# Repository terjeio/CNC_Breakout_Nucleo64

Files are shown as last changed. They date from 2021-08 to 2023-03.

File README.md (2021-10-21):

## CNC Breakout board for Nucleo-64 based development boards using ST morpho extension header

[grblHAL driver](https://github.com/grblHAL/STM32F4xx) support for [Nucleo F411RE](https://www.st.com/en/evaluation-tools/nucleo-f411re.html) and [Nucleo F446RE](https://www.st.com/en/evaluation-tools/nucleo-f446re.html) development boards.

**NOTE:** design files are in [KiCad 5](http://www.kicad.org/) format!

**Features:**

* Four layer board

* 4-axis motor support with separate enable for all axes.

* On-board sockets for Polulu \(A4998 and DRV8825\) or Trinamic \(TMC2130 or TMC5160 - SPI mode, TMC2209 - UART mode\) style motor driver modules.

* Opto-coupled limit and signal inputs (X, Y, Z, A, Probe, Reset/E-Stop, Door, Feed Hold and Cycle Start).

* Opto-coupled signal outputs \(Spindle on, Spindle direction, Flood, Mist, Aux0 and Aux1\).
Outputs are open drain \(ULN2003\) capable of draining 500mA, enough to drive most relays directly.

* Jumper selectable drive voltage for inputs and outputs, either 5V internally supplied or 5-30V externally supplied. 
If externally supplied inputs and outputs can be made galvanically isolated from the controller via jumper settings.

* 5V buffered PWM output for spindle speed control.

* Optional optocoupled DC spindle output, can be made galvanically isolated via jumper setting. External supply voltage limited to rating of filtering capacitor C7 (max. 30V).

* I2C port with jumper selectable drive voltage \(3.3V or 5V\). This is complemented with a 5V tolerant input pin that may be used as an interrupt source, eg. for the strobe signal from a I2C-based keypad.

* Two GPIO ports, with two pins each. One is unbuffered and can be used for serial communincation, eg. for MPG or VFD control. One is input only and has 5V tolerant pins.

* Optional on-board EEPROM/FRAM for persistent storage of settings.

* SPI based SD-card interface. If not in use some or all pins may be used as GPIO or as a generic SPI interface with one chip select line, depending on motor drivers used.

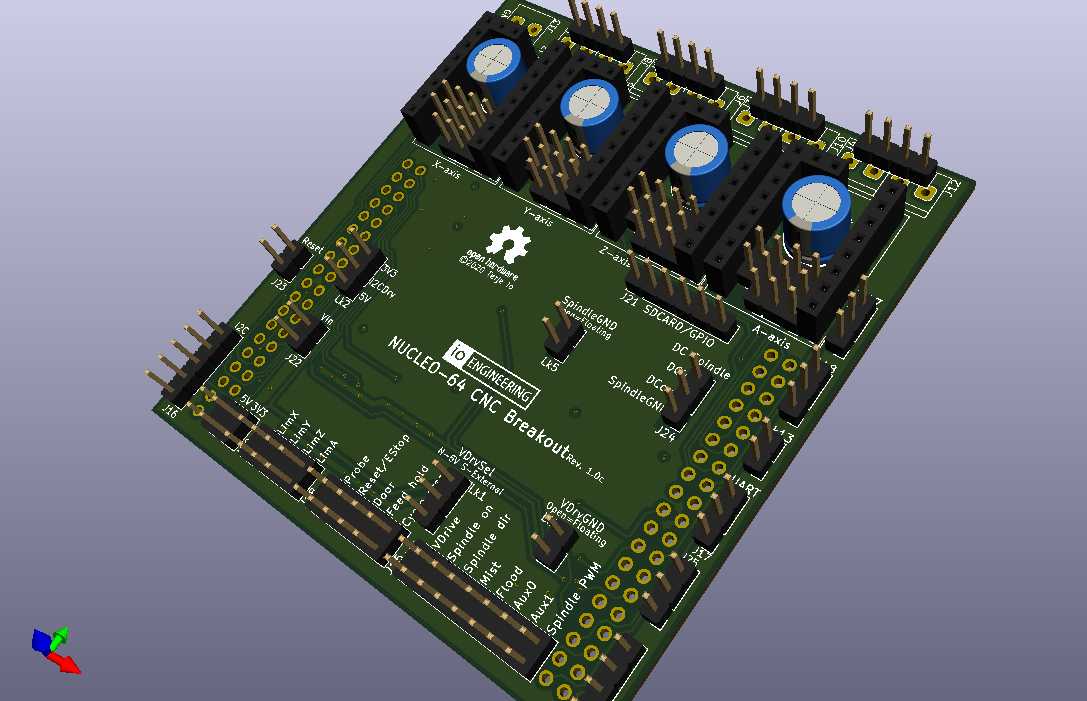
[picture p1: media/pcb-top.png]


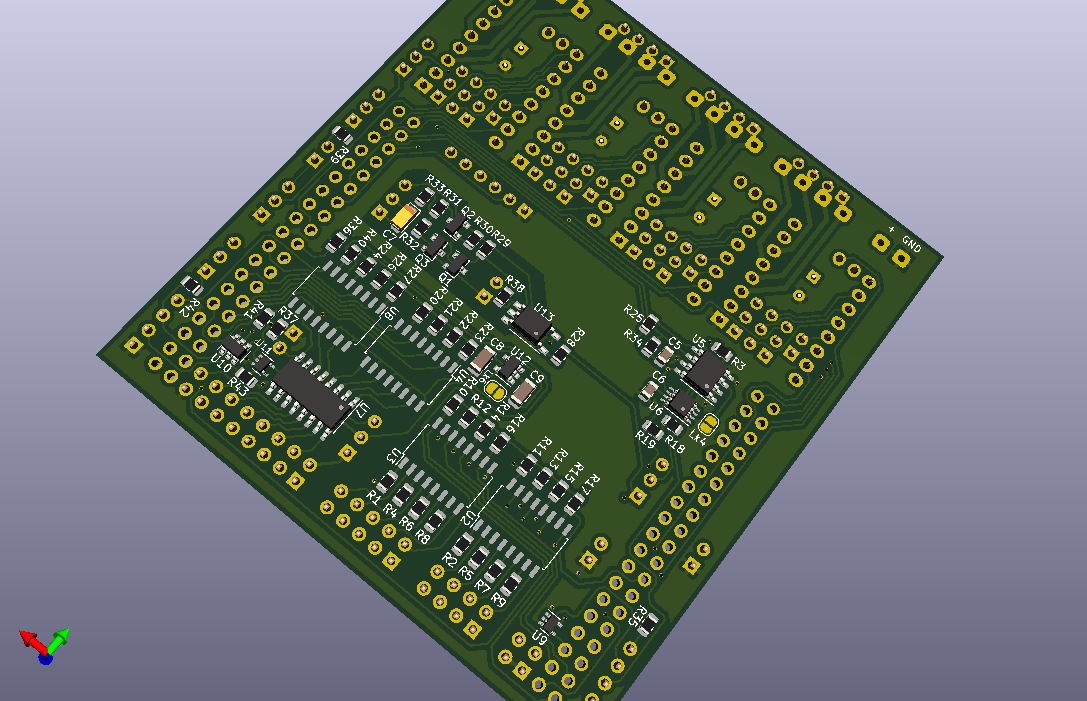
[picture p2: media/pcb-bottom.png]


---

I have a number of _bare_ boards available:

* 1.0 \(preliminary version\): 7 pcs. These do not support Trinamic drivers in SPI/UART mode and has a couple of correctable routing errors in the spindle PWM -> spindle DC circuit. Price: shipping at cost.

* 1.0b: 2 pcs. Price: EUR 5/pcs + shipping at cost. These are missing a pullup resistor for the keypad strobe input - this _may_ affect operation of the keypad plugin. Easy to add externally.

These boards are gold plated \(ENIG finish\).

* 1.0c: \(current version\) Not yet available.

I do not plan to offer populated boards as either I have to solder them myself \(will be expensive\) or place an order for ready made boards \(with only SMD components soldered\).  
A redesign is likely required for ready made boards as some of the components may not be available from the standard selection offered by e.g. [JLPCB](https://jlcpcb.com/).

It would be great if someone would get populated boards made and offered for sale as I am currently not prepared to do that.

---

2021-08-22

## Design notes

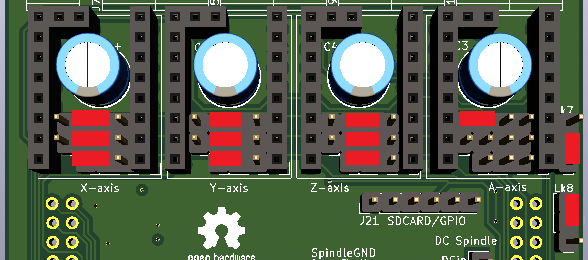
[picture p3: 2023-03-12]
media/TMC_SPI_mode_3motors.png

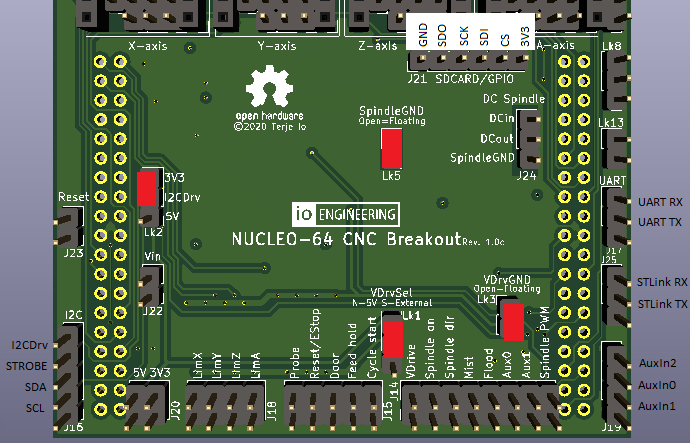
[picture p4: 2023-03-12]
media/Basic.png

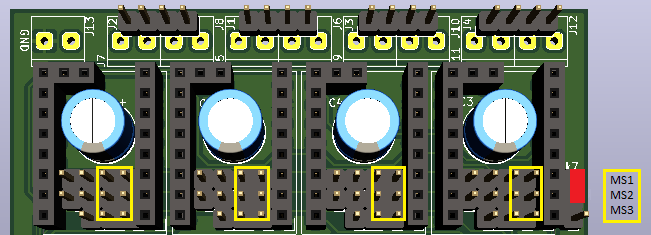
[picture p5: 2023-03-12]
media/Normal.png

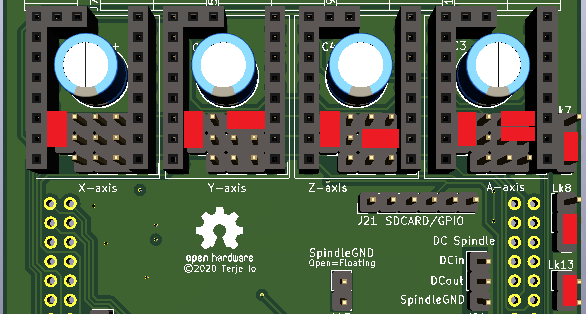
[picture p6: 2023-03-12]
media/TMC_UART_mode.png

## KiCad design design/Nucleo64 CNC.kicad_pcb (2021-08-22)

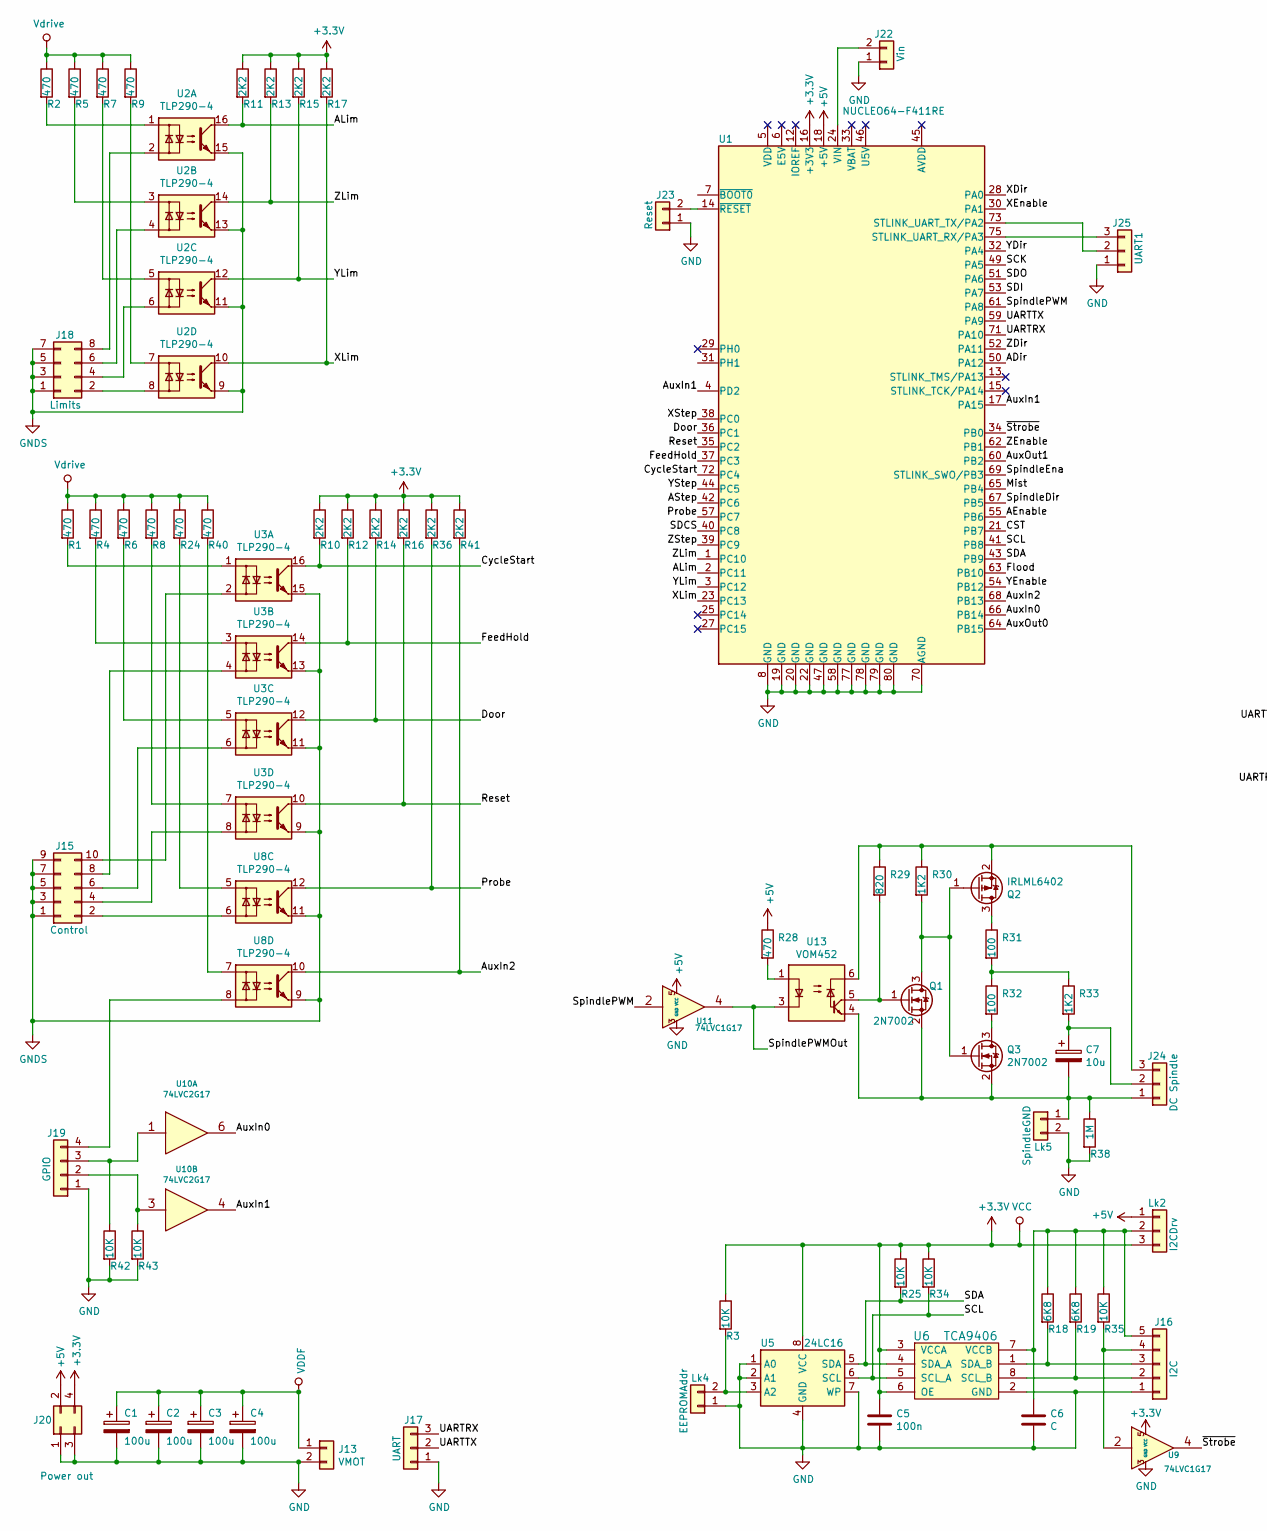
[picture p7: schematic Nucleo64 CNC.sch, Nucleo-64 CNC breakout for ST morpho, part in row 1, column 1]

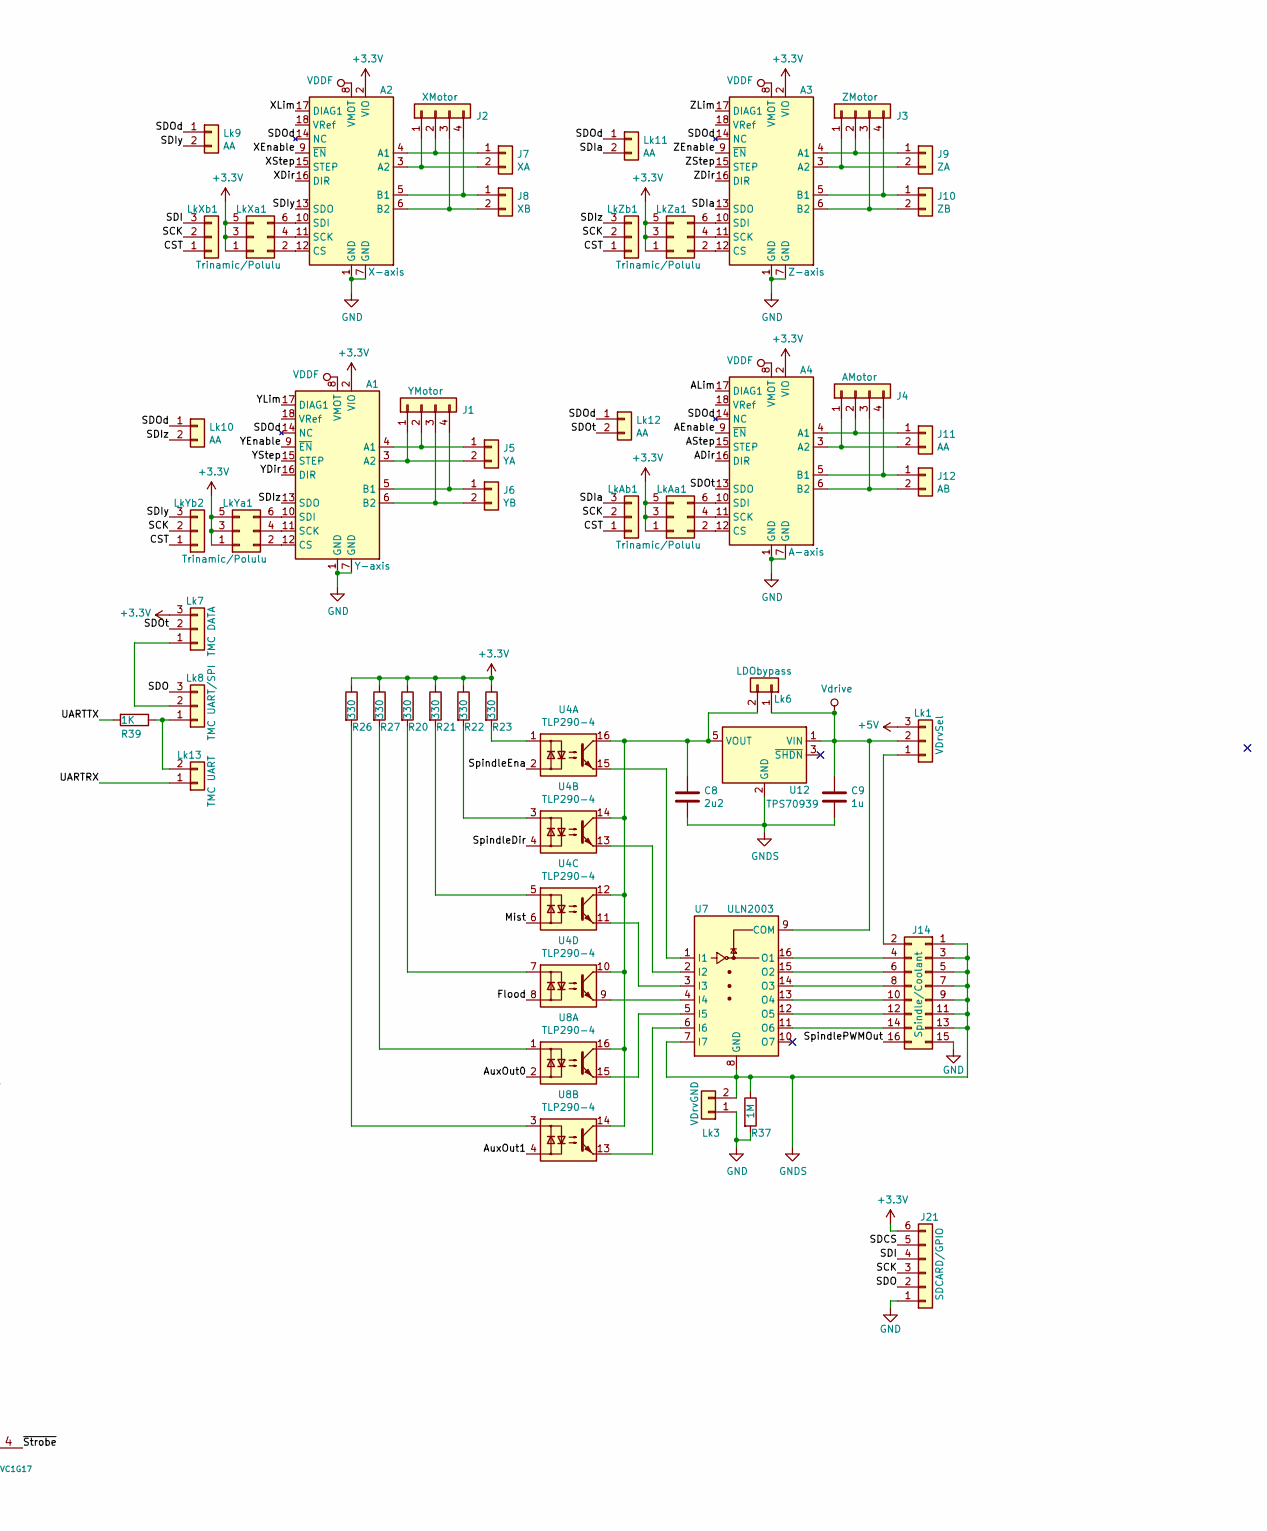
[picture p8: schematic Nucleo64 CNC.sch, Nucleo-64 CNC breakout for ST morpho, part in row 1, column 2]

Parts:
A1: Y-axis; SilentStepStick_TMC2130
A2: X-axis; SilentStepStick_TMC2130
A3: Z-axis; SilentStepStick_TMC2130
A4: A-axis; SilentStepStick_TMC2130
C1, C2, C3, C4: 100u; CP_Radial_D8.0mm_P3.50mm
C5: 100n; C_0805_2012Metric
C6: C; C_0805_2012Metric
C7: 10u; CP_EIA-3216-10_Kemet-I
C8: 2u2; C_1206_3216Metric
C9: 1u; C_1206_3216Metric
J1: YMotor; PinHeader_1x04_P2.54mm_Vertical
J2: XMotor; PinHeader_1x04_P2.54mm_Vertical
J3: ZMotor; PinHeader_1x04_P2.54mm_Vertical
J4: AMotor; PinHeader_1x04_P2.54mm_Vertical
J5: YA; CONN_PWR_2P_3.5MM_CAMBLOCK
J6: YB; CONN_PWR_2P_3.5MM_CAMBLOCK
J7: XA; CONN_PWR_2P_3.5MM_CAMBLOCK
J8: XB; CONN_PWR_2P_3.5MM_CAMBLOCK
J9: ZA; CONN_PWR_2P_3.5MM_CAMBLOCK
J10: ZB; CONN_PWR_2P_3.5MM_CAMBLOCK
J11: AA; CONN_PWR_2P_3.5MM_CAMBLOCK
J12: AB; CONN_PWR_2P_3.5MM_CAMBLOCK
J13: VMOT; CONN_PWR_2P_3.5MM_CAMBLOCK
J14: Spindle/Coolant; PinHeader_2x08_P2.54mm_Vertical
J15: Control; PinHeader_2x05_P2.54mm_Vertical
J16: I2C; PinHeader_1x05_P2.54mm_Vertical
J17: UART; PinHeader_1x03_P2.54mm_Vertical
J18: Limits; PinHeader_2x04_P2.54mm_Vertical
J19: GPIO; PinHeader_1x04_P2.54mm_Vertical
J20: Power out; PinHeader_2x02_P2.54mm_Vertical
J21: SDCARD/GPIO; PinHeader_1x06_P2.54mm_Vertical
J22: Vin; PinHeader_1x02_P2.54mm_Vertical
J23: Reset; PinHeader_1x02_P2.54mm_Vertical
J24: DC Spindle; PinHeader_1x03_P2.54mm_Vertical
J25: UART1; PinHeader_1x03_P2.54mm_Vertical
Lk1: VDrvSel; PinHeader_1x03_P2.54mm_Vertical
Lk2: I2CDrv; PinHeader_1x03_P2.54mm_Vertical
Lk3: VDrvGND; PinHeader_1x02_P2.54mm_Vertical
Lk4: EEPROMAddr; SolderJumper-2_P1.3mm_Open_RoundedPad1.0x1.5mm
Lk5: SpindleGND; PinHeader_1x02_P2.54mm_Vertical
Lk6: LDObypass; SolderJumper-2_P1.3mm_Open_RoundedPad1.0x1.5mm
Lk7: TMC DATA; PinHeader_1x03_P2.54mm_Vertical
Lk8: TMC UART/SPI; PinHeader_1x03_P2.54mm_Vertical
Lk9, Lk10, Lk11, Lk12: AA; PinHeader_1x02_P2.54mm_Vertical
Lk13: TMC UART; PinHeader_1x02_P2.54mm_Vertical
LkAa1: Trinamic/Polulu; PinHeader_2x03_P2.54mm_Vertical
LkAb1: PinHeader_1x03_P2.54mm_Vertical
LkXa1: Trinamic/Polulu; PinHeader_2x03_P2.54mm_Vertical
LkXb1: PinHeader_1x03_P2.54mm_Vertical
LkYa1: Trinamic/Polulu; PinHeader_2x03_P2.54mm_Vertical
LkYb2: PinHeader_1x03_P2.54mm_Vertical
LkZa1: Trinamic/Polulu; PinHeader_2x03_P2.54mm_Vertical
LkZb1: PinHeader_1x03_P2.54mm_Vertical
Q1, Q3: 2N7002; SOT-23
Q2: IRLML6402; SOT-23
R1, R2, R4, R5, R6, R7, R8, R9, R24, R28, R40: 470; R_0805_2012Metric
R3, R25, R34, R35, R42, R43: 10K; R_0805_2012Metric
R10, R11, R12, R13, R14, R15, R16, R17, R36, R41: 2K2; R_0805_2012Metric
R18, R19: 6K8; R_0805_2012Metric
R20, R21, R22, R23, R26, R27: 330; R_0805_2012Metric
R29: 820; R_0805_2012Metric
R30, R33: 1K2; R_0805_2012Metric
R31, R32: 100; R_0805_2012Metric
R37, R38: 1M; R_0805_2012Metric
R39: 1K; R_0805_2012Metric
U1: NUCLEO64-F411RE; ST_Morpho_Connector_64_STLink
U2, U3, U4, U8: TLP290-4; SOP-16_4.55x10.3mm_P1.27mm
U5: 24LC16; SOIC-8_3.9x4.9mm_P1.27mm
U6: TCA9406; SSOP-8_2.95x2.8mm_P0.65mm
U7: ULN2003; SOIC-16_3.9x9.9mm_P1.27mm
U9, U11: 74LVC1G17; SOT-353_SC-70-5
U10: 74LVC2G17; SOT-23-6
U12: TPS70939; SOT-23-5
U13: VOM452; MFSOP6-5_4.4x3.6mm_P1.27mm

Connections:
+3V3: A1.2 (VIO), A2.2 (VIO), A3.2 (VIO), A4.2 (VIO), C5.1, J20.4, J21.6, Lk2.3, Lk7.3, LkAa1.1, LkAa1.3, LkAa1.5, LkXa1.1, LkXa1.3, LkXa1.5, LkYa1.1, LkYa1.3, LkYa1.5, LkZa1.1, LkZa1.3, LkZa1.5, R3.1, R10.1, R11.1, R12.1, R13.1, R14.1, R15.1, R16.1, R17.1, R20.1, R21.1, R22.1, R23.1, R25.1, R26.1, R27.1, R34.1, R36.1, R41.1, U1.16 (+3V3), U5.8 (VCC), U6.3 (VCCA), U6.6 (OE), U9.5 (VCC), U10.5 (VCC)
+5V: J20.2, Lk1.3, Lk2.1, R28.1, U1.18 (+5V), U11.5 (VCC)
/ADir: A4.16 (DIR), U1.50 (PA12)
/AEnable: A4.9 (~EN), U1.55 (PB6)
/ALim: A4.17 (DIAG1), R11.2, U1.2 (PC11), U2.16
/AStep: A4.15 (STEP), U1.42 (PC6)
/AuxIn0: U1.66 (PB14), U10.6
/AuxIn1: U1.4 (PD2), U1.17 (PA15), U10.4
/AuxIn2: R41.2, U1.68 (PB13), U8.10
/AuxOut0: U1.64 (PB15), U8.2
/AuxOut1: U1.60 (PB2), U8.4
/CST: LkAb1.1, LkXb1.1, LkYb2.1, LkZb1.1, U1.21 (PB7)
/CycleStart: R10.2, U1.72 (PC4), U3.16
/Door: R14.2, U1.36 (PC1), U3.12
/FeedHold: R12.2, U1.37 (PC3), U3.14
/Flood: U1.63 (PB10), U4.8
/Mist: U1.65 (PB4), U4.6
/Probe: R36.2, U1.57 (PC7), U8.12
/Reset: R16.2, U1.35 (PC2), U3.10
/SCK: J21.3, LkAb1.2, LkXb1.2, LkYb2.2, LkZb1.2, U1.49 (PA5)
/SCL: R34.2, U1.41 (PB8), U5.6 (SCL), U6.5 (SCL_A)
/SDA: R25.2, U1.43 (PB9), U5.5 (SDA), U6.4 (SDA_A)
/SDCS: J21.5, U1.40 (PC8)
/SDI: J21.4, LkXb1.3, U1.53 (PA7)
/SDIa: A3.13 (SDO), Lk11.2, LkAb1.3
/SDIy: A2.13 (SDO), Lk9.2, LkYb2.3
/SDIz: A1.13 (SDO), Lk10.2, LkZb1.3
/SDO: J21.2, Lk8.3, U1.51 (PA6)
/SDOd: A1.14 (NC), A2.14 (NC), A3.14 (NC), A4.14 (NC), Lk9.1, Lk10.1, Lk11.1, Lk12.1
/SDOt: A4.13 (SDO), Lk7.2, Lk12.2
/SpindleDir: U1.67 (PB5), U4.4
/SpindleEna: U1.69 (STLINK_SWO/PB3), U4.2
/SpindlePWM: U1.61 (PA8), U11.2
/SpindlePWMOut: J14.16, U11.4, U13.3 (C)
/UARTRX: J17.3, Lk13.1, U1.71 (PA10)
/UARTTX: J17.2, R39.2, U1.59 (PA9)
/XDir: A2.16 (DIR), U1.28 (PA0)
/XEnable: A2.9 (~EN), U1.30 (PA1)
/XLim: A2.17 (DIAG1), R17.2, U1.23 (PC13), U2.10
/XStep: A2.15 (STEP), U1.38 (PC0)
/YDir: A1.16 (DIR), U1.32 (PA4)
/YEnable: A1.9 (~EN), U1.54 (PB12)
/YLim: A1.17 (DIAG1), R15.2, U1.3 (PC12), U2.12
/YStep: A1.15 (STEP), U1.44 (PC5)
/ZDir: A3.16 (DIR), U1.52 (PA11)
/ZEnable: A3.9 (~EN), U1.62 (PB1)
/ZLim: A3.17 (DIAG1), R13.2, U1.1 (PC10), U2.14
/ZStep: A3.15 (STEP), U1.39 (PC9)
/~Strobe: U1.34 (PB0), U9.4
GND: A1.1 (GND), A1.7 (GND), A2.1 (GND), A2.7 (GND), A3.1 (GND), A3.7 (GND), A4.1 (GND), A4.7 (GND), C1.2, C2.2, C3.2, C4.2, C5.2, C6.2, J13.2, J14.15, J16.1, J17.1, J19.1, J20.1, J20.3, J21.1, J22.1, J23.1, J25.1, Lk3.1, Lk4.1, Lk5.2, R37.2, R38.2, R42.2, R43.2, U1.8 (GND), U1.19 (GND), U1.20 (GND), U1.22 (GND), U1.47 (GND), U1.58 (GND), U1.70 (AGND), U1.77 (GND), U1.78 (GND), U1.79 (GND), U1.80 (GND), U5.1 (A0), U5.2 (A1), U5.4 (GND), U5.7 (WP), U6.2 (GND), U9.3 (GND), U10.2 (GND), U11.3 (GND)
GNDS: C8.2, C9.2, J14.1, J14.3, J14.5, J14.7, J14.9, J14.11, J14.13, J15.1, J15.3, J15.5, J15.7, J15.9, J18.1, J18.3, J18.5, J18.7, Lk3.2, R37.1, U2.9, U2.11, U2.13, U2.15, U3.9, U3.11, U3.13, U3.15, U7.7 (I7), U7.8 (GND), U8.9, U8.11, U12.2 (GND)
unnamed: A1.3 (A2), J1.1, J5.2
unnamed: A1.4 (A1), J1.2, J5.1
unnamed: A1.5 (B1), J1.4, J6.1
unnamed: A1.6 (B2), J1.3, J6.2
unnamed: A1.10 (SDI), LkYa1.6
unnamed: A1.11 (SCK), LkYa1.4
unnamed: A1.12 (CS), LkYa1.2
unnamed: A2.3 (A2), J2.1, J7.2
unnamed: A2.4 (A1), J2.2, J7.1
unnamed: A2.5 (B1), J2.4, J8.1
unnamed: A2.6 (B2), J2.3, J8.2
unnamed: A2.10 (SDI), LkXa1.6
unnamed: A2.11 (SCK), LkXa1.4
unnamed: A2.12 (CS), LkXa1.2
unnamed: A3.3 (A2), J3.1, J9.2
unnamed: A3.4 (A1), J3.2, J9.1
unnamed: A3.5 (B1), J3.4, J10.1
unnamed: A3.6 (B2), J3.3, J10.2
unnamed: A3.10 (SDI), LkZa1.6
unnamed: A3.11 (SCK), LkZa1.4
unnamed: A3.12 (CS), LkZa1.2
unnamed: A4.3 (A2), J4.1, J11.2
unnamed: A4.4 (A1), J4.2, J11.1
unnamed: A4.5 (B1), J4.4, J12.1
unnamed: A4.6 (B2), J4.3, J12.2
unnamed: A4.10 (SDI), LkAa1.6
unnamed: A4.11 (SCK), LkAa1.4
unnamed: A4.12 (CS), LkAa1.2
unnamed: C6.1, J16.5, Lk2.2, R18.1, R19.1, R35.1, U6.7 (VCCB)
unnamed: C7.1, J24.2, R33.2
unnamed: C7.2, J24.1, Lk5.1, Q1.2 (S), Q3.2 (S), R38.1, U13.4 (GND)
unnamed: C8.1, Lk6.2, U4.10, U4.12, U4.14, U4.16, U8.14, U8.16, U12.5 (VOUT)
unnamed: J14.2, Lk1.1
unnamed: J14.4, U7.16 (O1)
unnamed: J14.6, U7.15 (O2)
unnamed: J14.8, U7.14 (O3)
unnamed: J14.10, U7.13 (O4)
unnamed: J14.12, U7.12 (O5)
unnamed: J14.14, U7.11 (O6)
unnamed: J15.2, U8.6
unnamed: J15.4, U3.8
unnamed: J15.6, U3.6
unnamed: J15.8, U3.4
unnamed: J15.10, U3.2
unnamed: J16.2, R19.2, U6.8 (SCL_B)
unnamed: J16.3, R18.2, U6.1 (SDA_B)
unnamed: J16.4, R35.2, U9.2
unnamed: J18.2, U2.8
unnamed: J18.4, U2.6
unnamed: J18.6, U2.4
unnamed: J18.8, U2.2
unnamed: J19.2, R43.1, U10.3
unnamed: J19.3, R42.1, U10.1
unnamed: J19.4, U8.8
unnamed: J22.2, U1.24 (VIN)
unnamed: J23.2, U1.14 (~RESET)
unnamed: J24.3, Q2.2 (S), R29.1, R30.1, U13.6 (VCC)
unnamed: J25.2, U1.73 (STLINK_UART_TX/PA2)
unnamed: J25.3, U1.75 (STLINK_UART_RX/PA3)
unnamed: Lk4.2, R3.2, U5.3 (A2)
unnamed: Lk7.1, Lk8.2
unnamed: Lk8.1, Lk13.2, R39.1
unnamed: Q1.1 (G), R29.2, U13.5 (VO)
unnamed: Q1.3 (D), Q2.1 (G), Q3.1 (G), R30.2
unnamed: Q2.3 (D), R31.1
unnamed: Q3.3 (D), R32.2
unnamed: R1.2, U3.1
unnamed: R2.2, U2.1
unnamed: R4.2, U3.3
unnamed: R5.2, U2.3
unnamed: R6.2, U3.5
unnamed: R7.2, U2.5
unnamed: R8.2, U3.7
unnamed: R9.2, U2.7
unnamed: R20.2, U4.7
unnamed: R21.2, U4.5
unnamed: R22.2, U4.3
unnamed: R23.2, U4.1
unnamed: R24.2, U8.5
unnamed: R26.2, U8.3
unnamed: R27.2, U8.1
unnamed: R28.2, U13.1 (A)
unnamed: R31.2, R32.1, R33.1
unnamed: R40.2, U8.7
unnamed: U4.9, U7.4 (I4)
unnamed: U4.11, U7.3 (I3)
unnamed: U4.13, U7.2 (I2)
unnamed: U4.15, U7.1 (I1)
unnamed: U7.5 (I5), U8.15
unnamed: U7.6 (I6), U8.13
VDDF: A1.8 (VMOT), A2.8 (VMOT), A3.8 (VMOT), A4.8 (VMOT), C1.1, C2.1, C3.1, C4.1, J13.1
Vdrive: C9.1, Lk1.2, Lk6.1, R1.1, R2.1, R4.1, R5.1, R6.1, R7.1, R8.1, R9.1, R24.1, R40.1, U7.9 (COM), U12.1 (VIN)

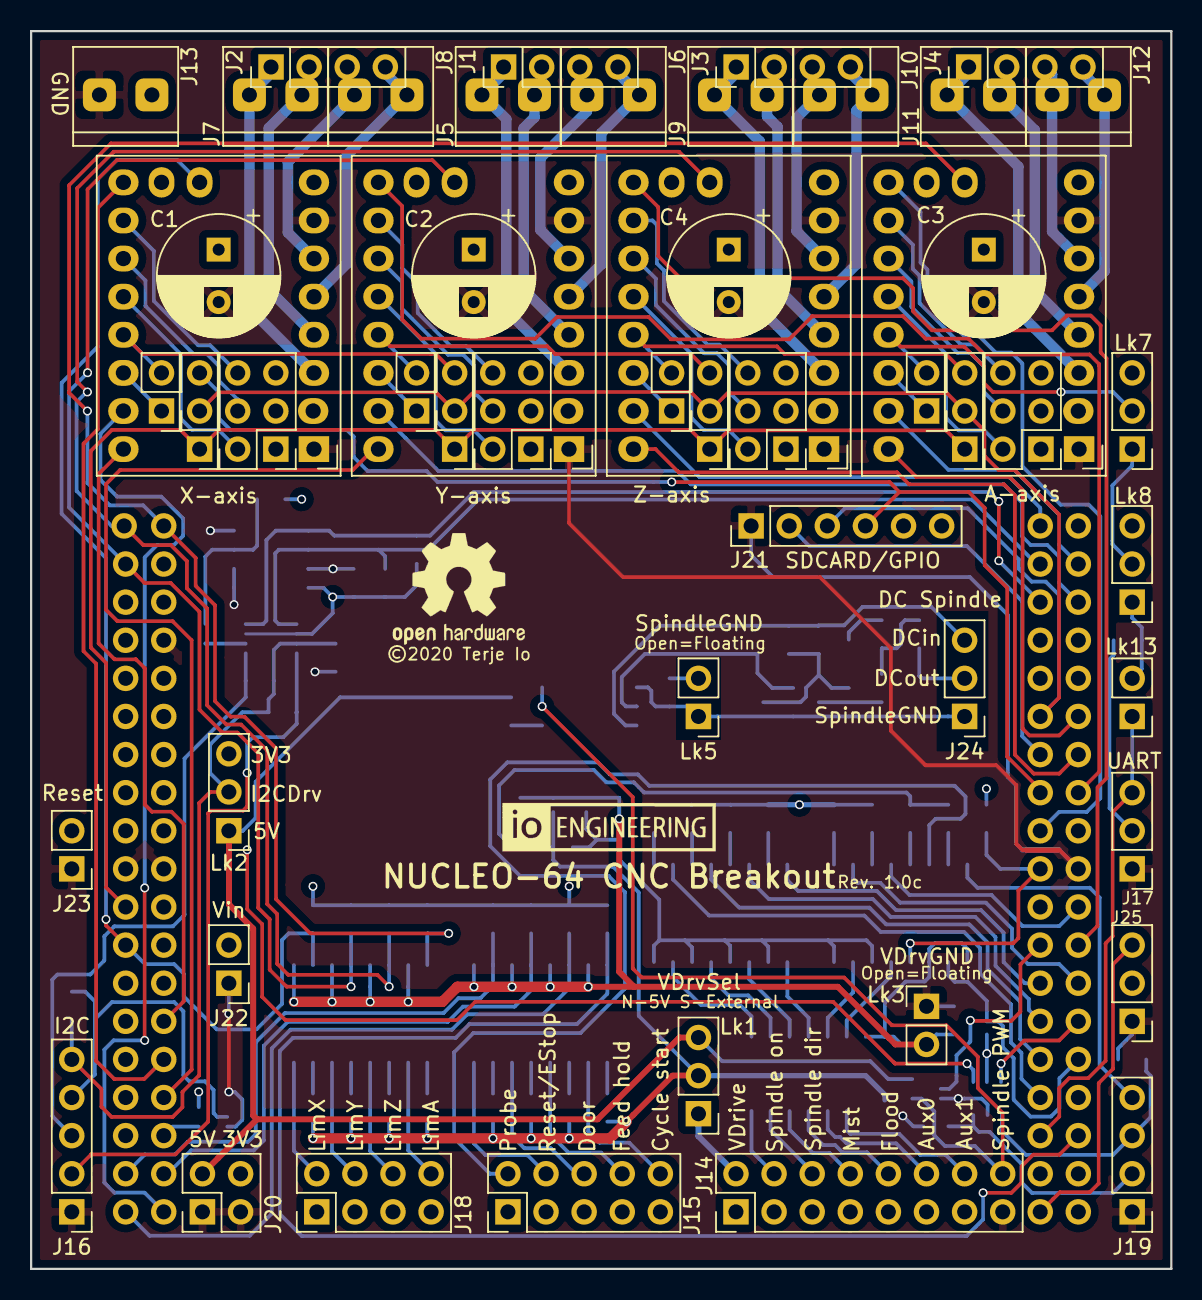
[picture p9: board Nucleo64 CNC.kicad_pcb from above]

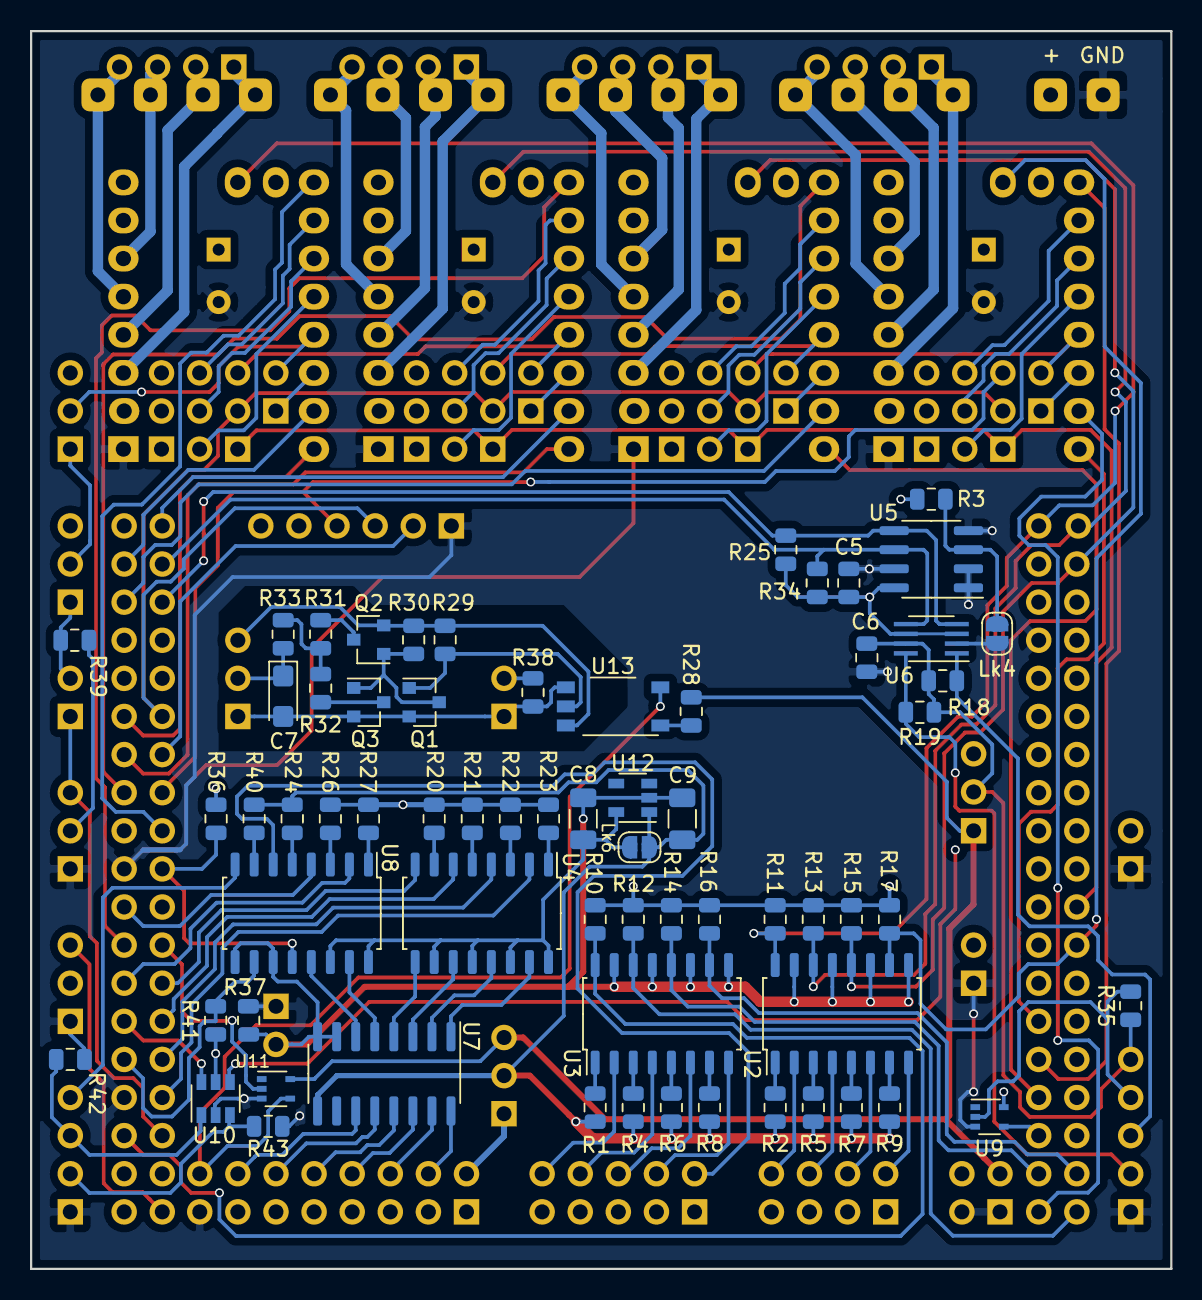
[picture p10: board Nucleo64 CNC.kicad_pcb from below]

Board: 4 copper layers, 76.0 x 82.5 mm, 118 parts (65 on the bottom side), 143 nets.

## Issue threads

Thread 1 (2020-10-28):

Not a problem but might scare some...

phil-barrett, 2020-10-28:
Using kICAD 5.1.6 (or later) you will get a waring when opening up the .sch. It appears to be ok, though.
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

terjeio, 2020-10-28:
Thanks, will check my libraries and update as needed. Warning can be safely ignored - schematic will then use the symbols cached with the project.

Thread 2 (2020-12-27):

Great job! Can I buy these boards somewhere?

darkfibre-nl, 2020-12-27:
Hi Terje,

As I happen to have a Nucleo with a STM32F411RE onboard, I figured I might as well put it to good use running grblHAL.

Did you, or anyone else had these made, and perhaps have a few to spare?
As I am not too familiar with Kicad beyond the title of the program, is there a parts list I might use as a shoppinglist?

Festive regards!

terjeio, 2020-12-27:
I have a few _unpopulated_ boards to spare from the first batch. There is a fixable layout error for PWM > 0 - 10V spindle control. Trinamic drivers controlled by UART (TMC2209) or SPI (TMC2130) cannot be used either. A couple of Euros per board and postage at cost is reasonable? I can add a mylar solder paste stencil too if required.

I have not yet made a parts list but that can be extracted from the KiCad files, on my todo list.

I am about to make a new batch with Trinamic driver support and improved PWM -> 0 - 10V spindle control (faster optocoupler, layout fix). Sensorless homing will not be supported for TMC2209 due to lack of pins. TMC2130 _may_ get support for sensorless homing as these have an open drain output that be wire-or'ed together.

Happy holidays!

jappiemike, 2021-08-21:
Hello Terjeio, thank you so much for the outstanding work you are doing, a real labour of love. I'm keen to buy a couple of populated boards when you have them available.
Cheers
Mike

terjeio, 2021-08-22:
> I'm keen to buy a couple of populated boards when you have them available.

I am not planning to sell populated boards as I have to solder up the few unpopulated ones I have myself. See the bottom of the [readme](https://github.com/terjeio/CNC_Breakout_Nucleo64/blob/main/README.md) for details.

Yesterday I finally completed verification of the new batch mentioned above, I have just updated the repo with the latest version that has one resistor added for the I2C keypad strobe input.

jappiemike, 2021-08-22:
OK, I have a bit of soldering experience but not surface mount, can you please give me a guesstimate price on 3 boards shipped to Brisbane Australia.

Cheers Mike
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

nebulorum, 2022-05-12:
Ran into this project and was curious if the boards (Rev B or C) still and how to get them if they still exist? I'm in the EU.

terjeio, 2022-05-13:
@nebulorum They are still available, payment is via Paypal. I need the quantity to calculate postage - will post a comment with the Paypal account then. Nota thate the boards are bare - you have to get the components and solder them yourself.

nebulorum, 2022-05-14:
Would work for me but we need a way to direct message. Issues are not a good place to put personal data :)

I was also wondering if you can't use a Group By (like in mechanical keyboard) to do a run of Rev C with SMD already added.

terjeio, 2022-05-17:
> Issues are not a good place to put personal data

My email/paypal address: terjeio@online.no

> I was also wondering if you can't use a Group Buy (like in mechanical keyboard) to do a run of Rev C with SMD already added.

If someone is willing to do that it is ok for me.

customsolutions, 2023-11-22:
I know ive been in the other discussions, but I just found this. Are there any bare boards avail? Partslist? Did you get pwm issue resolved I saw a few posts back?

terjeio, 2023-11-22:
@customsolutions I still have a few boards available. A BOM can be generated from the KiCad project, I made one earlier but do not have access to it now as I am on an extended holiday.
The PWM issue is with the PWM > DC conversion circuit on the first revision of the board and can be fixed by modifying it.

customsolutions, 2023-11-22:
Reach out after you get back, and we can discuss further.... enjoy.

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

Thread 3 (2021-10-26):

C

M10CUBE, 2021-10-26:
M10CUBE format CNC Brakeout Nucleo64

M10CUBE, 2021-10-30:
OK @terjeio KiCAD now reads the schematic .
You are using the connector CONN_PWR_2P_3.5MM_CAMBLOCK
The one I find is this:
https://www.aliexpress.com/item/33029158756.html?spm=a2g0o.store_pc_groupList.8148356.6.13457f61oGaiBR
Problem is that can not have to side by side. Is your connector without the plastic in the sides?
Otherwise I have to order the 4P version
I bought for M10CUBE  from this supplier many types but all was 3.81mm

terjeio, 2021-10-30:
> You are using the connector CONN_PWR_2P_3.5MM_CAMBLOCK

Either that or 2.54mm pin headers. User choice.

> Problem is that can not have to side by side. Is your connector without the plastic in the sides?

Not sure what you mean by this, the connectors I use can be slided into each other. I have 2P and 3P variants which can be joined to whatever number of pins I want. Or do you mean 2.54mm pin headers with white plastic (shroud?) around them which some steppers comes with a mating plug for?

> I bought for M10CUBE from this supplier many types but all was 3.81mm

You can change the PCB to match those? Not sure if there is enough room though.

M10CUBE, 2021-10-30:
Can you please point me to the supplier for your connector to colied with
others so as to form a continuous one? so i can only do 2p and 3 p like
you. I do not want to change the pcb at the moment concerning the
connectors.  thanks

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

--
Vasilis Vorrias

Electronics and Automation

M10CUBE project: https://hackaday.io/project/171770-m10cube
GitLAB : https://gitlab.com/m10cube/m10
email: ***@***.*** ***@***.***>
Skype: vorrias_home
Phone home: +302421049323 <+30%202421%20049323>

Against GM food

terjeio, 2021-11-01:
I am waiting for new delivery - nearly four months now so I do not think I should link to that supplier (from china via ebay).
However, I found it on [Aliexpress](https://www.aliexpress.com/wholesale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), it is [this](https://www.aliexpress.com/item/2029152736.html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) type.

M10CUBE, 2021-11-01:
Four months! we had that problem in Greece last year but now delivering is starting normal.
So I choose the discrete ones since dificult to source the ones that go side by side. But I will look for it
I order from the supplier you pointed out from Aliexpress since my supplier has only packets of 50.
since I have many  many 2P, 3P, 4P 3.5mm plugs (left over from our motion drive installations) I paced order for the corresponding sockets in packet of 30 angled because these can be used as straight by straightening. (not the other way around). To see how it will go and I will order more variation in the future. I may switch to the 3.5mm instead of 3.81mm for our M10CUBE.
Now
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
I only want to connect I2C on the M10CUBE+CNC_Breakout_Nucleo64 and sent it for FAB. So until the connectors arrival I will have the PCBs on my LAB to give it a try

M10CUBE, 2021-11-05:
Hi @terjeio
Recently Dr Dalaris from techexplorations.com found M10CUBE idea interesting and wants to make a podcast about it.

https://community.techexplorations.com/c/makers-club/kicad-like-a-pro-3rd-edition-update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

As you know KiCAD 6 announcing date is in December.
I'm thinking it is a good idea when I will speak in podcast to announce as a case study the mix of the
a) CNC_Breakout_Nucleo64  by @terjeio  + M10CUBE
b) Pi Pico CNC @Phil Barrett + M10CUBE

That will give publicity to all the topics involved specially the GRBLHAL project
I will invite Phil Barrett as well from PicoCNC project to help me move the new version he is preparing into the M10CUBE format.
The way I see we have the following advantages by doing that.
1 - KiCAD 6 design
2 - M10CUBE framework
3 - Nucleo64 and Raspberry Pi Pico CNC designs on board (both fits nicely into 90 X 90 mm)
4 - Ready for GRBLHAL
5 - Final design can be integrated with others M10CUBE modules like I/Os already done (V1 but I am doing V2 now)

All that without sacrificing any design done so far with Nucleo64 CNC or Raspberry Pi Pico CNC but only adding all the M10CUBE features.

Dr Dalmaris placed the podcast on December but I am thinking to move it from next year so to have time to discuss and document the idea better.

The only thing you need to jump on M10CUBE is only that:

1 - to have 90x90mm for PCB dimension (on places where I/O connectors are you can go up to 100mm)
2 - to have mounting holes for M3 screws located 4x4mm from the edges of the 90 x 90 mm PCB
3 - on one side on specific location a 40 pin Raspberry connector must be located. Even if you have it unconnected

I already have a template made (KiCA6 nightly builds) to help out the transition.
https://drive.google.com/drive/folders/1f1UmG2nwTirFiiY7XVGedgxhAJYgD1Qi?usp=sharing
On the coming M10CUBE podcast both designs (Nucleo64 CNC and Raspberry Pi Pico CNC) will explored as successful case studies.
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

So I really want to hear from you on that.

terjeio, 2021-11-06:
Interesting, my design is open hardware so feel free to modify it as you please. I see that you have already added the Pi header above. BTW in addition to routing I2C to that header you may want to route UARTTX/UARTRX as well? For I2C you have included the STROBE signal (from U9/pin2)?

Note I have no intention of selling it myself, and the component choices I've made is not well suited for assembly by a manufacturer such as JLPCB? Some, such as the optocouplers, has to be substituted with similar ones from the manufacturers parts list?
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
terjeio, 2021-11-25:
> I am Only confused about UART. Your suggestion is to use that on PA2/PA3 (J25) ?

No, I wrote UART2 then explained what UART1 is connected to. If connecting to UART1 (PA2/PA3) then you have to remove SB13/SB14 on the Nucleo board which will disable serial over USB. If this is what you want then use UART1.
Be aware the UART2 port is wired to the stepper drivers if they are TMC2209s configured for UART mode. UART2 cannot be used if so.

The strobe pin on the Pi should be set up as open drain output, this will allow other devices using the strobe input to be connected to J16.

M10CUBE, 2021-11-25:
Thanks @terjeio . I am thinking the UART2 as a better solution. In real life external drivers with your plug in interface cards will be used or the internal ones in  SPI mode. And see how it will go. We can always change later on a new version if something goes terribly wrong. I am moving to complete the proposed changes and the submit.

M10CUBE, 2021-11-26:
Hi @terjeio . I did all the suggested changes and looks nothing broken. As I said before sketch is not connected to PCB because it is not annotated (I will solve that later).
Board looks OK (even 3.5 mm horizontal connectors looks right on the edge). If you bother to have check it before sending for production it will be nice.
I could not move your logo to the right position but I will fix that before fabrication. Zip file is in KICAD6 but PDF inside as well
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
[M10NC01-10.zip](https://github.com/terjeio/CNC_Breakout_Nucleo64/files/7610709/M10NC01-10.zip)
Thanks for helping me

terjeio, 2021-11-28:
It looks better now, good to go.

M10CUBE, 2021-11-29:
Thanks @terjeio I made final clean up
- Manage to put your logo (some labels are rotated but in place)
- on your schematic only small addition necessary to connect the two designs
- No connection with 3.3v. That is not necessary since it is output fro RASPI and they recommend not to connect
- Schematic is annotated but still did all changes without importing net list . (fear of messing up. maybe In an other version )
Design is uploaded to JLCPCB but not ordered yet since I am preparing some changes to I/O boards this week.
**Please tell me if you want to send you some M10NUCLEO CNCboards and I/O boards so to test your GRBLHAL I2C I/O.**
As I said before I3C is already in the market and as infineon informed me they are considering I3C interface. MPUs are starting touse I3C already. It will be fantastic for bus driven modular controllers.
When that comes it will be easy to convert M10CUBE I/O to I3C
Before the end of the year I will introduce a full working PLC using M10CUBE concept. On that M10 CNC board will play a significant role.
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
[M10NC01-10.zip](https://github.com/terjeio/CNC_Breakout_Nucleo64/files/7618200/M10NC01-10.zip)

M10CUBE, 2022-01-06:
Hi @terjeio . I just finished 2 new I/O boards for use with M10CUBE platform plus your design.
1 - INPUT 8X24V, OUTPUT  8XSSR
https://hackaday.io/project/171770-m10cube/log/202093-m10cube-i2c-input-8x24v-output-8xssr-triac
2 - OUTPUT 8XRELAY MODULE
https://hackaday.io/project/171770-m10cube/log/202092-m10cube-i2c-8xrelay-module
3 - NUCLEO CNC your design ported to M10CUBE
https://hackaday.io/project/171770-m10cube/log/202097-m10cube-nucleo64-cnc

Went for PCB fabrication together with the above M10NUCLEO CNC board, wait to receive them and solder everything on board.
New I/O boards with any combination is easy to design based on some previews designs. Practically no limits on the I/Os on board.
While waiting for the boards there is time now to consider building a GRBLHAL based on Raspberry Pico board. That design will probably continue on Phil-Barrett space (if he agrees of course). My intention is to keep the four step drivers and spindle control from your design. Then add some more step drivers (up to four or any number [M10NC02-10.pdf](https://github.com/terjeio/CNC_Breakout_Nucleo64/files/7824266/M10NC02-10.pdf) pin-out will permit me).
Final board will have [M10NC02-10.pdf](https://github.com/terjeio/CNC_Breakout_Nucleo64/files/7824266/M10NC02-10.pdf), 8xsteper drivers and 1PWM for spindle control (isolated). All other I/O will move to M10CUBE I2C I/O modules.
First impression is here:
https://hackaday.io/project/171770-m10cube/log/202098-m10cube-pico-cnc

Here comes your experience on using the Trinamic/Polulu drivers. Since it is my first design looking at your circuit I can not configure the way you connect the SPI (SDI, SDO, SCK, CS) signals. Looks like all having same CS together. Is the select is done using Enable signal on pin 9? . And what are the SDIy, SDIa, SDIz, SDOt signals on SDO inputs?

All this info is needed not only to help me on the PICO design but for building your board when I receive it
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

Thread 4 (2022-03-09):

Optocoupled DC Spindle max voltage

Volksolive, 2022-03-09:
Hi Terjeio,

You mention in the readme that the max voltage for the optocoupled DC spindle output is limited by C7 = 30V but there is actually 2 other limiting factor.

-  The high side P mosfet transistor IRLML6402 has a VDS max of 20V and VGS max is 12V.
- The low side N mosfet transistor 2N7002 VGS max is 20V.

So max voltage should be 12V because of the P mosfet but can't be more than 20V if the P mosfet is replaced by another ref. because transistors rarely have more than 20V VGS max.

BTW what is that output intended to drive? because the 2N7002 does not provide that much power? (115mA const.)

terjeio, 2022-03-09:
Oops - I have to pay more attention to details.

> BTW what is that output intended to drive? because the 2N7002 does not provide that much power? (115mA const.)

A relatively high impedance input for VFD spindle RPM control, R33/C7 act as a LP filter and R33 will limit the drive current available. A typical voltage range is 0-10V.

Volksolive, 2022-03-09:
oh yes ok! I think the DC spindle word got me confused! I thought the intent was to drive a DC motor directly...

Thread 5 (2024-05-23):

CNC PENDANT and ETHERNET?

M10CUBE, 2024-05-23:
Hi terjeio
I know I have been missing a long time but other obligations took me away.

I am re-working with your CNC BREAKEOUT NUCLEO 64. I have 2 questions please.
1 - Any idea of putting a CNC pendant box? DIY or ready.  What correction do I have to do in firmware and how.
2 - Any progress of putting Ethernet on CNC BREAKEOUT NUCLEO 64?

Well been wishes for everybody here

Thanks

terjeio, 2024-06-25:
1 - MPG mode, possibly in combination with the keypad plugin is [available](https://github.com/grblHAL/STM32F4xx/blob/2cfeccf4053071133d90ec02e0faef7706b92d94/Inc/my_machine.h#L84-L89).
2 - [Available](https://github.com/grblHAL/STM32F4xx/blob/2cfeccf4053071133d90ec02e0faef7706b92d94/Inc/my_machine.h#L79) - see the [board map](https://github.com/grblHAL/STM32F4xx/blob/master/boards/st_morpho_map.h).

Note that due to limited number of pins there are restrictions on which options can be enabled together.

M10CUBE, 2024-06-27:
Thanks @terjeio .  Is this part of the GRBLHAL code? If not how can I embed it?
A long time ago using your directions I uploaded the code via a web interface but I forgotten how.
If I understated correctly I must use some RX, TX pins in BREAKEOUT NUCLEO to communicate with my custom MPG board.
I am not sure witch pins are the correct t ones.

I am looking at your GRBL_MPG_DRO_BoosterPack  project. I see that you progress it a lot but still no keyboard on Pico
I am thinking to do the MPG totally using Raspberry Pico board(s).
I saw the discussion about the 2 Picos and liked it.
I may start with a very simple Pico design sending MPG to BREAKEOUT NUCLEO  and stick to the discussion...
If any suggestions happy to hear.
Thanks again

terjeio, 2024-06-28:
> I am not sure witch pins are the correct t ones.

[These](https://github.com/grblHAL/STM32F4xx/blob/2cfeccf4053071133d90ec02e0faef7706b92d94/boards/st_morpho_map.h#L52).

> I am thinking to do the MPG totally using Raspberry Pico board(s).

I have added automatic programming of the MSP430 to the Pico code so it can be added as just any other componet. If you want to use a Pico for keyboard scanning/LED control the MSP430 code has to be ported to it.

M10CUBE, 2024-07-02:
I have started a discussion for an MPG using only 2 Picos. It is an aproach started 2 years ago with only some hors spent on the idea.
Considering the interest on that I think it will be an interesting approach, useful to the community.
https://github.com/grblHAL/RP2040/discussions/92#discussion-6889273
Please comment if you have some spare time. It is nice to know that I am on the right track
Thanks

terjeio, 2024-07-04:
Continues at this [discussion](https://github.com/grblHAL/RP2040/discussions/92).

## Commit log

2020-11-22 Updated to version sent for small prototype batch
    Design and board map file to be verified with this batch.
    [Nucleo64 CNC.kicad_pcb, Nucleo64 CNC.sch]
2021-08-22 Updated to v1.0c
    [Nucleo64 CNC.kicad_pcb, Nucleo64 CNC.sch]
2021-10-21 Updated kicad link
2023-03-12 Added board configs

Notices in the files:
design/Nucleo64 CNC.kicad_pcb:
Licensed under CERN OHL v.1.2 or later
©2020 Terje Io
